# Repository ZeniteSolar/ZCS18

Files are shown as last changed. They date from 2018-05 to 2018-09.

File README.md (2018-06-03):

# ZCS18 - Zênite CAN! Shield 2018
The piece of hardware used in almost all modules in the boat of Zênite Solar Team on 2018.

## About

zenite_logo 

[Zênite Solar TEAM](https://github.com/ZeniteSolar) is an universitary project from [IFSC](http://www.ifsc.edu.br) focused on the development of a high performance solar boat for races and it aims to be completly open source.

- All the hardware was developed using [KiCad](http://kicad-pcb.org/);
- Simulations was done using [LTSpice](http://www.analog.com/en/design-center/design-tools-and-calculators/ltspice-simulator.html);
- Schematics are available [here][Schematic];
- BOM are available [here][BOM];

## Status

- [x] Simulations
- [x] Schematics
- [x] PCB
- [x] Fabrication
- [ ] Assembly
- [ ] Test
- [ ] Basic Firmware for reference

## Board View

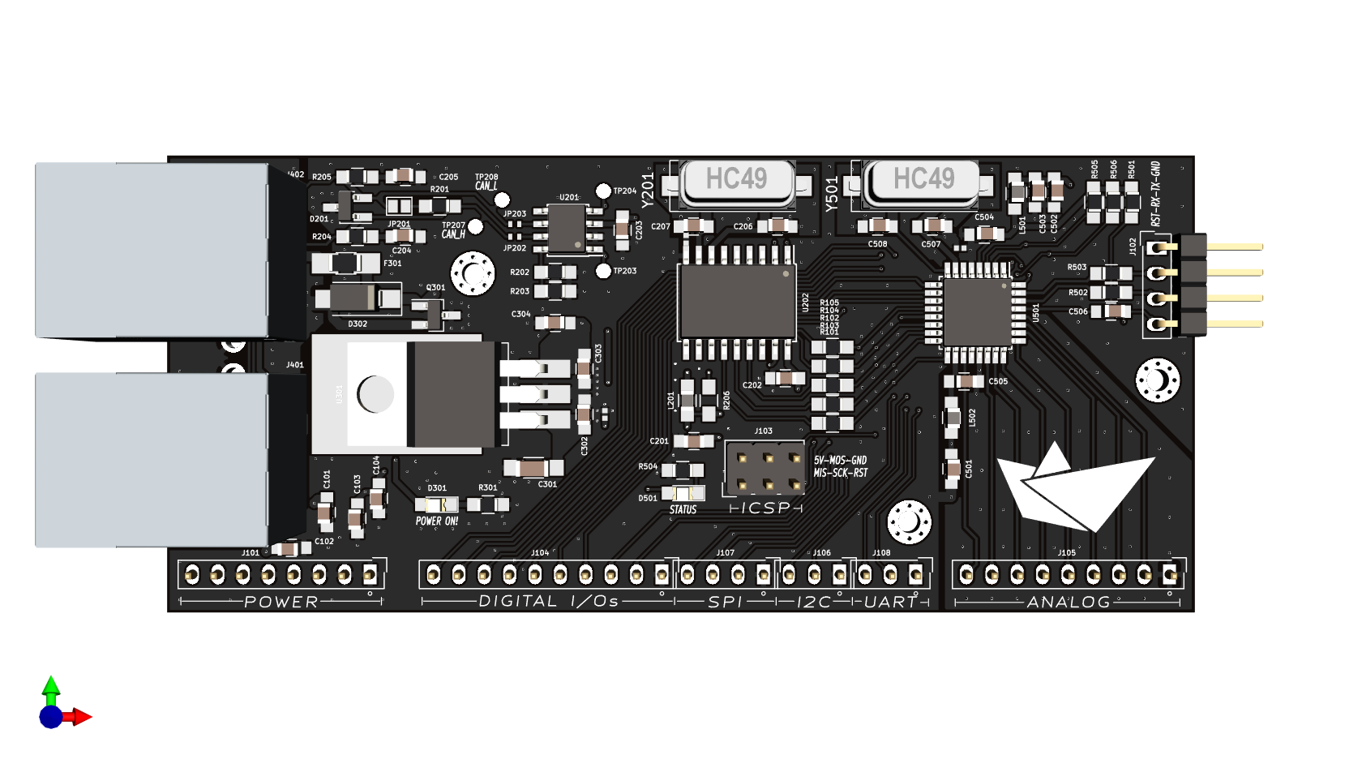
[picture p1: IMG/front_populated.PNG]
kicad3d_front_populated
 

***

[Schematic]: PDF/atmega_can_shield.pdf "Schematics"
[BOM]: PDF/BOM.pdf "Bill Of Materials"
[photo_front]: IMG/front.PNG "Fabricated Front"
[photo_back]: IMG/front.PNG "Fabricated Back"
[photo_front]: IMG/front.PNG "Populated Front"
[photo_back]: IMG/front.PNG "Populated Back"
[kicad3d_front]: IMG/front.PNG "Kicad Front"
[kicad3d_back]: IMG/back.PNG "Kicad Back"
[kicad3d_front_populated]: IMG/front_populated.PNG "Kicad Populated Front"
[kicad3d_back_populated]: IMG/back_populated.PNG "Kicad Populated Back"
[kicad3d_populated_angled]: IMG/populated_angled.PNG "Kicad Populated Board 3D View"
[zenite_logo]: https://avatars2.githubusercontent.com/u/8411347?s=100 "Zênite Solar Team Logo"

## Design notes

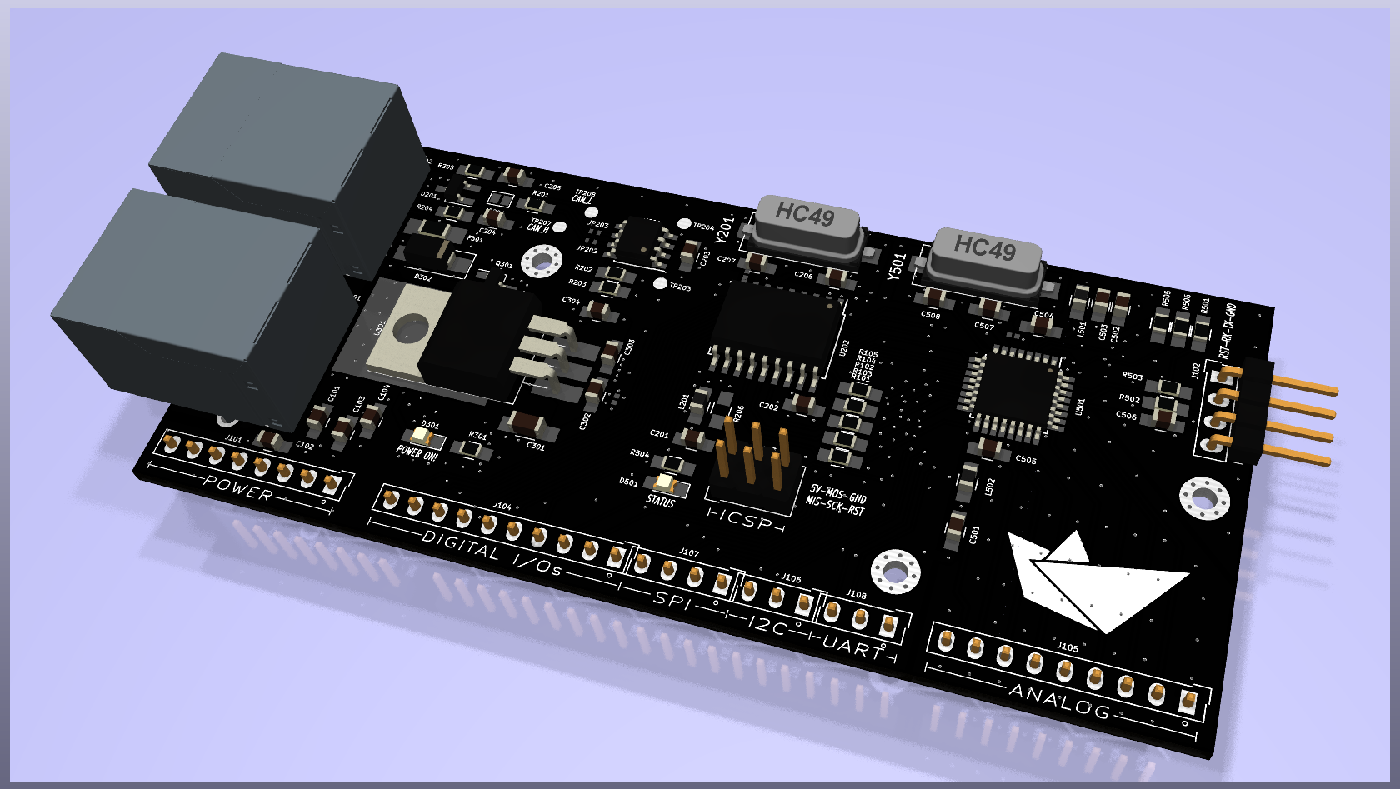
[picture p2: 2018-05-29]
IMG/populated_angled.PNG

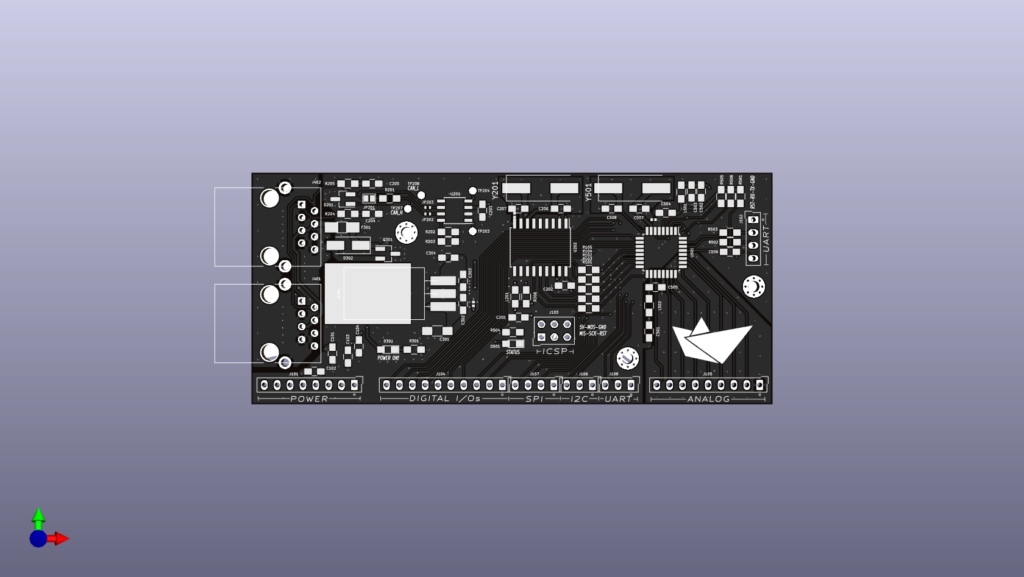
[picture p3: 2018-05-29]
IMG/front.PNG

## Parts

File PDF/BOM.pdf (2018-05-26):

atmega_can_shield_bom_João A.C.

CompPart | References | Value | Footprint | QTD Voltage
1 C_Small | | 100n | C_0805_HandSoldering | 12 >25V
2 CP1_Small | C301 | 10uF | C_1206_HandSoldering | 1 >25V
3 C_Small | C101 C103 C503 1u | C_0805_HandSoldering | 3 >25V
4 CP1_Small | C304 | 1uF | C_0805_HandSoldering | 1
5 C_Small | | 22pF | C_0805_HandSoldering | 4
6 C_Small | C204 C205 | 560p | C_0805_HandSoldering | 2
7LED_Small_ALT | D301 D501 | LED_RED | LED_0805_HandSoldering | 2
8 D_TVS | D302 | | D_SMA_Handsoldering | 1
9 D_TVS_x2_AAC | D201 | pesd1can | SOT-23_Handsoldering | 1
10 Fuse_Small | F301 | | Fuse_SMD1206_HandSolde | 1
11 CONN_01X09 | J105 | ANALOG | SL-109-X-XX_1x09 | 1
12 CONN_01X10 | J104 | DIGITAL I/Os SL-110-X-XX_1x10 | 1
13 CONN_01X03 | J106 | I2C | SL-103-X-XX_1x03 | 1
14 CONN_02X03 | J103 | ICSP | SDL-106-X-XX_2x03 | 1
15 GS2 | J201 J301 J501 | NetTie | \xc2\xb5NetTie-I_Connect | 3
16 RJ45 | J401 J402 | RJ45 | RJ45_YH59_01 | 2
17 CONN_01X04 | J107 | SPI | SL-104-X-XX_1x04 | 1
18 CONN_01X08 | J101 | SUPPLY | SL-108-X-XX_1x08 | 1
19 CONN_01X04 | J102 | USART | SL-104-X-XX_1x04 | 1
20 CONN_01X03 | J108 | USART | SL-103-X-XX_1x03 | 1
21 2-pole | open | | JP202 JP203 | 1
22Jumper_NO_Small JP201 | Termination GS2 | 1
23L_Core_Ferrite | L201 L501 L502 | 10uH | L_0805_HandSoldering | 3
24 Q_NMOS_GSD | Q301 | si2308cds | SOT-23_Handsoldering | 1
25 R_Small | 100 R_0805_HandSoldering | 7
26 R_Small | | 10k | R_0805_HandSoldering | 8
27 R_Small | R201 | 120 R_0805_HandSoldering | 1
28 R_Small | R502 R503 | 1k | R_0805_HandSoldering | 2
29 | U501 | | TQFP-32_7x7mm_Pitch0.8 | 1
30 | U202 | | SOIC-18W_7.5x11.6mm_Pi | 1
31 MCP2551-I_SN | U201 | MCP2561 | SOIC-8_3.9x4.9mm_Pitch1 | 1
32LM7805_TO220 | U301 | | TO-220_Horizontal_SMD | 1
33 Crystal_Small | Y201 Y501 | 16MHz | Crystal_SMD_HC49_4HSM | 2

C102 C104 C201
C202 C203 C302
C303 C501 C502
C504 C505 C506

C206 C207 C507
C508

TVS 24V
400W

500mA
resettable

Jumper_2_O
pen

R101 R102 R103
R104 R105 R204
R205
R202 R203 R206
R301 R501 R504
R505 R506

SRAM 512B
EEPROM
ATMEGA328P-AU_alt

ATMEGA328
P-AU_alt

MCP2515-E_ST-SOIC18

MCP2515-
E/ST-SOIC18

VXO7805-
1000

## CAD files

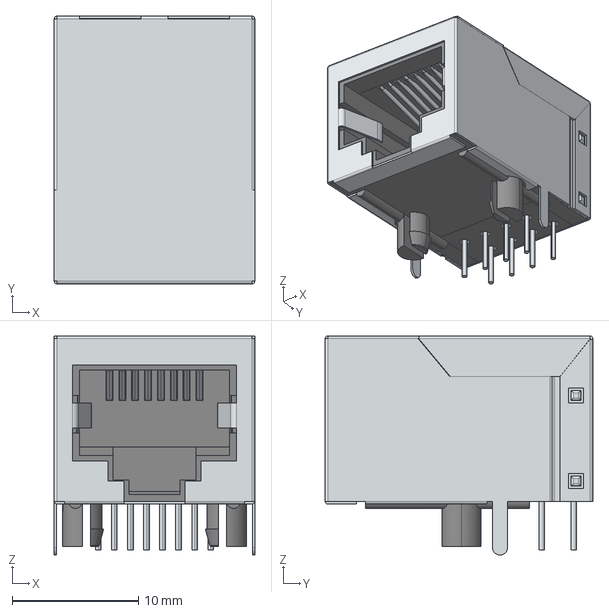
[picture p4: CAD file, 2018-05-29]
rj45.step
15.9 x 21.2 x 17.3 mm

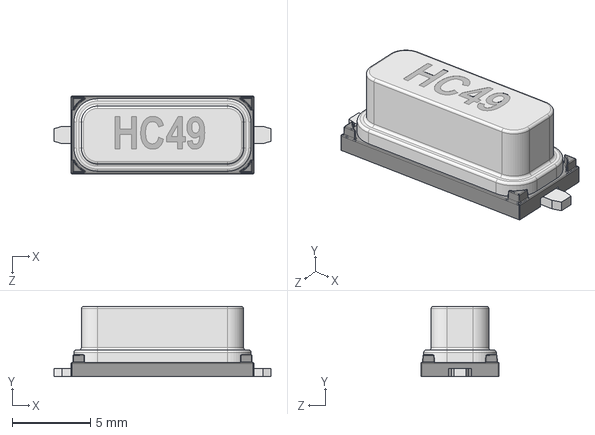
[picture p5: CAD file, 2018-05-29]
HC49.step
13.9 x 4.51 x 5.00 mm

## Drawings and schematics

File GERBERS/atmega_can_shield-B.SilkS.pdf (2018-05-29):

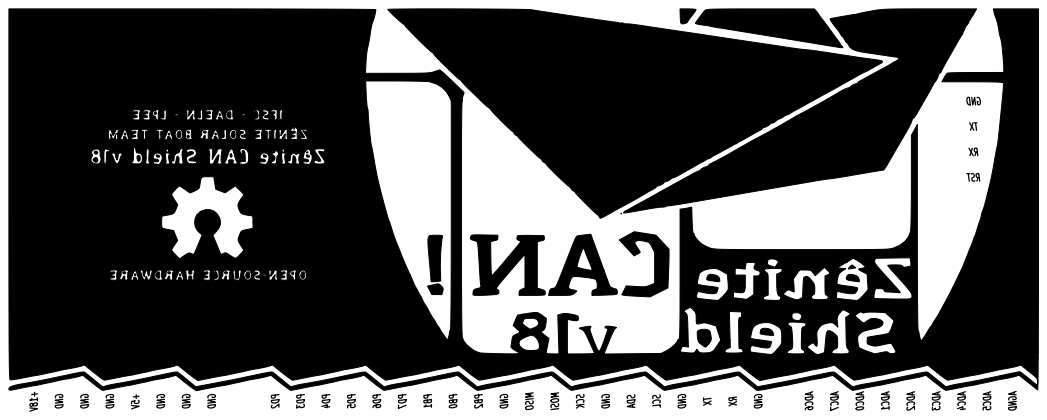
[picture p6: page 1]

TXRX GND ADC6 ADC7 ADC0 ADC1 ADC2 ADC3 ADC4 ADC5 +18V GND GND GND +5V GND GND GND GND GND AGND SCK SDA SCL TXRX PD2 PD3 PD4 PD5 PD6 PD7 PB1 PB0 PB2 GND MISO MOSI

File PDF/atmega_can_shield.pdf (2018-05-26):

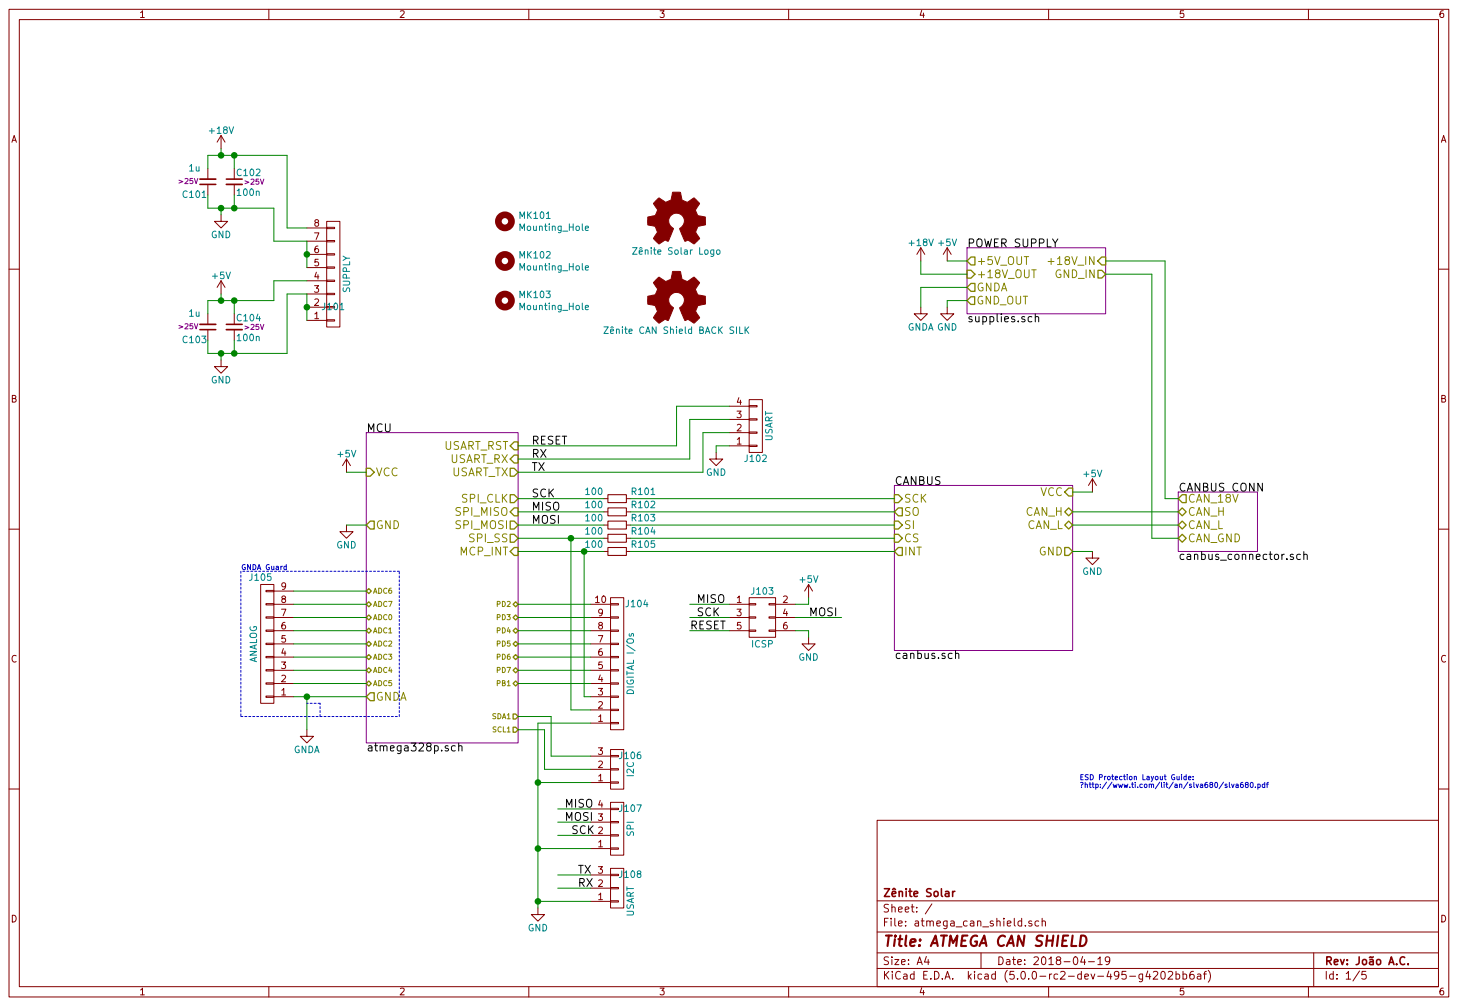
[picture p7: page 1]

Zênite Solar Logo Zênite CAN Shield BACK SILK

100 R102
100 R103

CAN_18V CAN_GND

ESD Protection Layout Guide:

File: atmega_can_shield.sch Sheet: / Zênite Solar

Id: 1/5 Title: ATMEGA CAN SHIELD

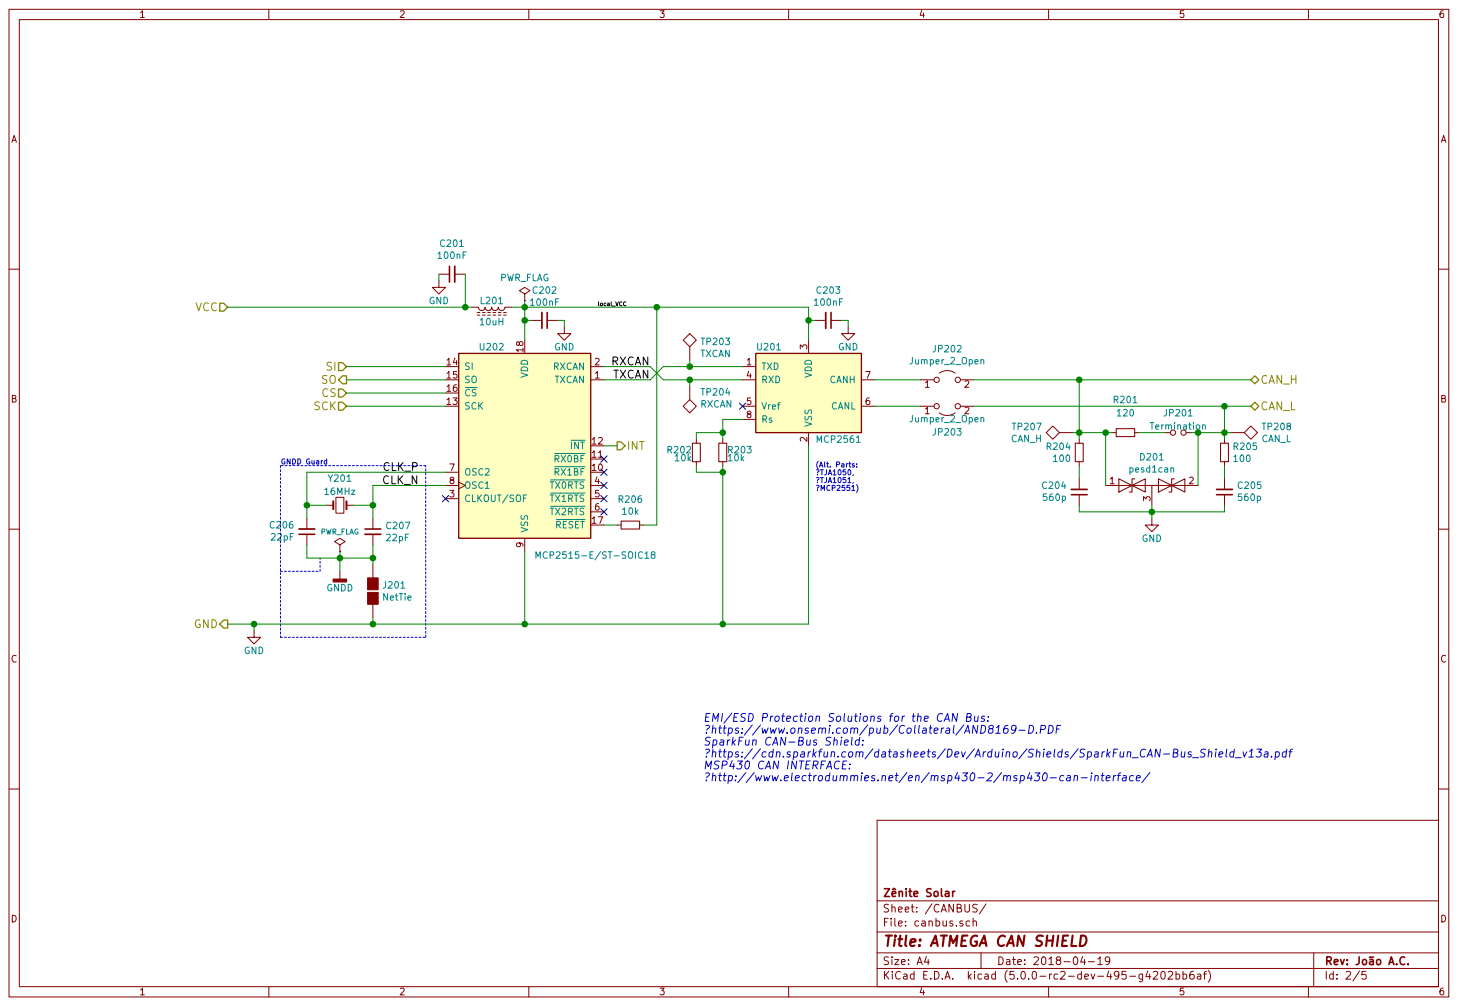
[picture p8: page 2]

3 RXD 4 Vref 5 CANL 6 CANH 7 Rs 8 U201 MCP2561 TXCAN
RXCAN

EMI/ESD Protection Solutions for the CAN Bus:
https://www.onsemi.com/pub/Collateral/AND8169-D.PDF
SparkFun CAN-Bus Shield:
https://cdn.sparkfun.com/datasheets/Dev/Arduino/Shields/SparkFun_CAN-Bus_Shield_v13a.pdf
MSP430 CAN INTERFACE:
http://www.electrodummies.net/en/msp430-2/msp430-can-interface/

File: canbus.sch Sheet: /CANBUS/ Zênite Solar

Id: 2/5 Title: ATMEGA CAN SHIELD

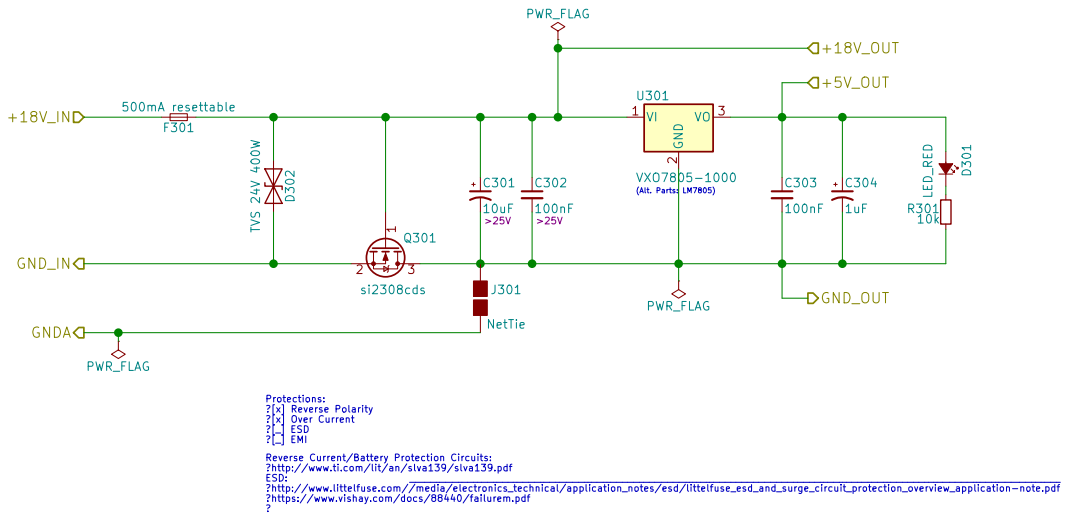
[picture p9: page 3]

si2308cds Reverse Current/Battery Protection Circuits:

https://www.vishay.com/docs/88440/failurem.pdf Protections:
[x] Reverse Polarity
[x] Over Current
[_] ESD

http://www.ti.com/lit/an/slva139/slva139.pdf ESD:
http://www.littelfuse.com//media/electronics_technical/application_notes/esd/littelfuse_esd_and_surge_circuit_protection_overview_application-note.pdf

File: supplies.sch Sheet: /POWER SUPPLY/ Zênite Solar

Id: 3/5 Title: ATMEGA CAN SHIELD

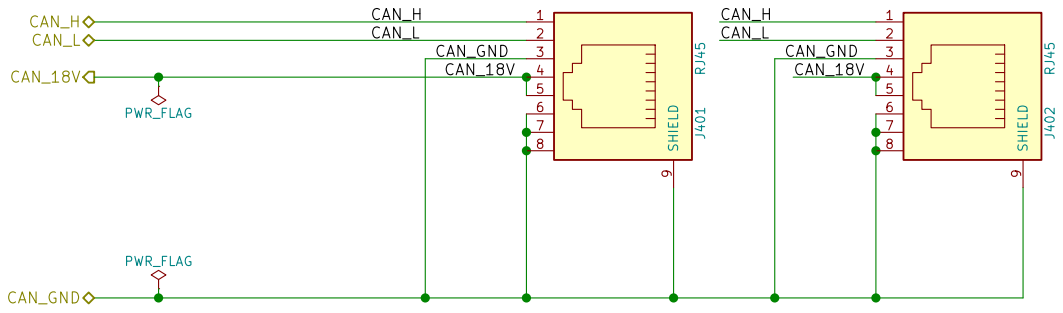
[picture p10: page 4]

File: canbus_connector.sch Sheet: /CANBUS CONN/ Zênite Solar

Id: 4/5 Title: ATMEGA CAN SHIELD

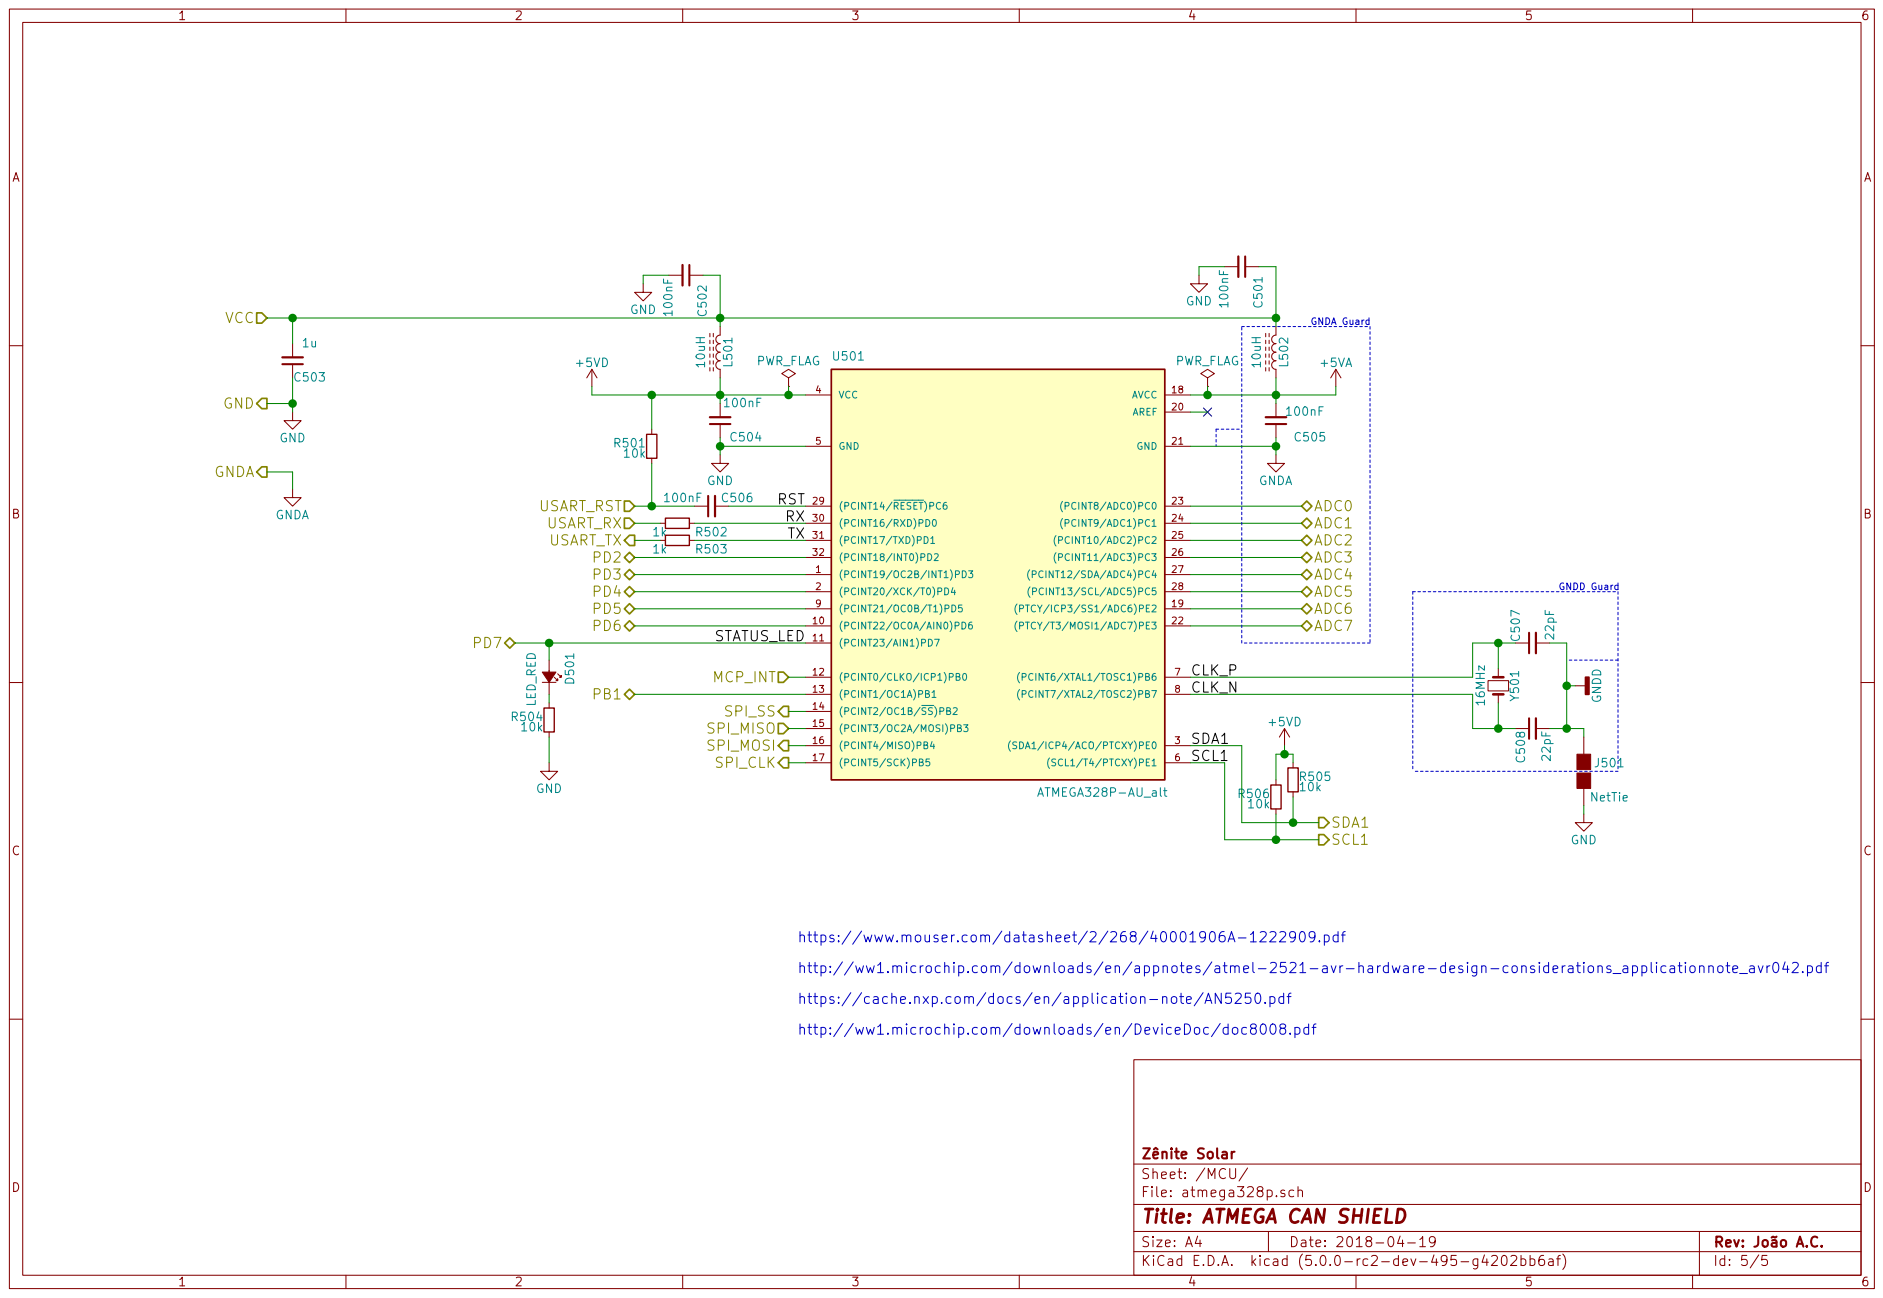
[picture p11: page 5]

https://www.mouser.com/datasheet/2/268/40001906A-1222909.pdf
http://ww1.microchip.com/downloads/en/appnotes/atmel-2521-avr-hardware-design-considerations_applicationnote_avr042.pdf
https://cache.nxp.com/docs/en/application-note/AN5250.pdf

Id: 5/5 Title: ATMEGA CAN SHIELD

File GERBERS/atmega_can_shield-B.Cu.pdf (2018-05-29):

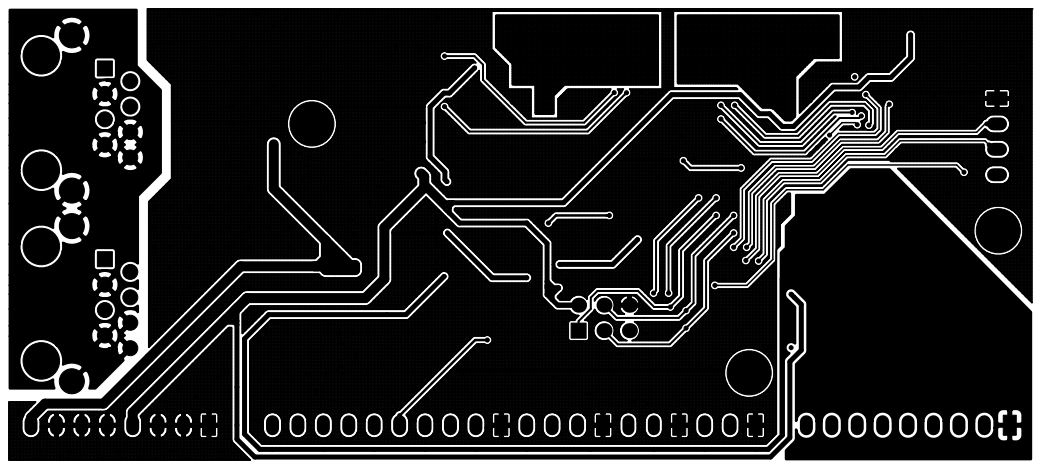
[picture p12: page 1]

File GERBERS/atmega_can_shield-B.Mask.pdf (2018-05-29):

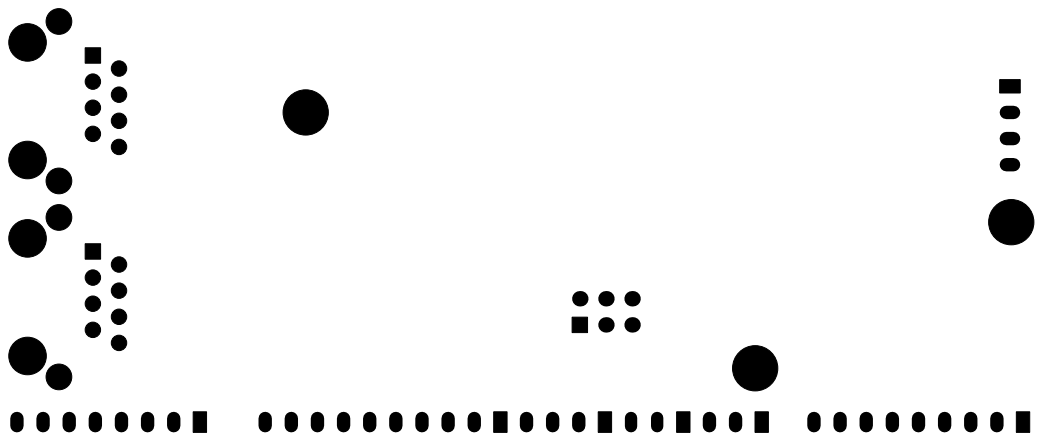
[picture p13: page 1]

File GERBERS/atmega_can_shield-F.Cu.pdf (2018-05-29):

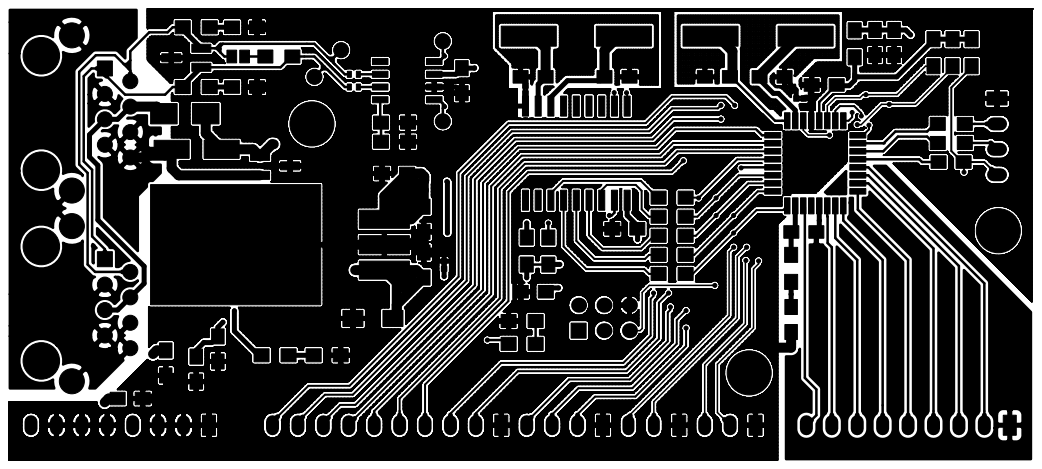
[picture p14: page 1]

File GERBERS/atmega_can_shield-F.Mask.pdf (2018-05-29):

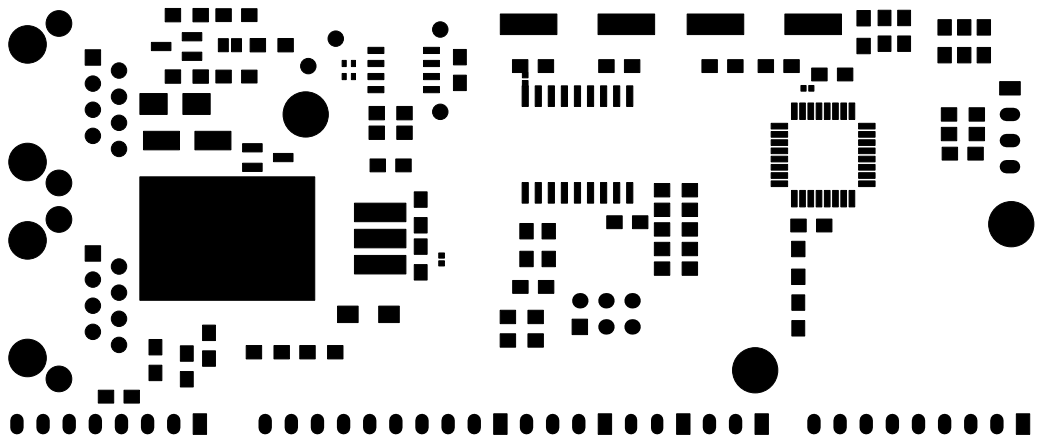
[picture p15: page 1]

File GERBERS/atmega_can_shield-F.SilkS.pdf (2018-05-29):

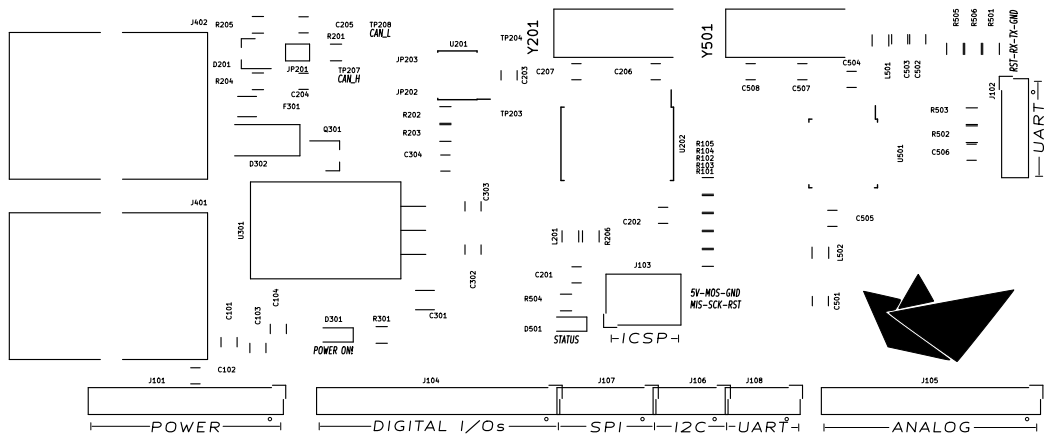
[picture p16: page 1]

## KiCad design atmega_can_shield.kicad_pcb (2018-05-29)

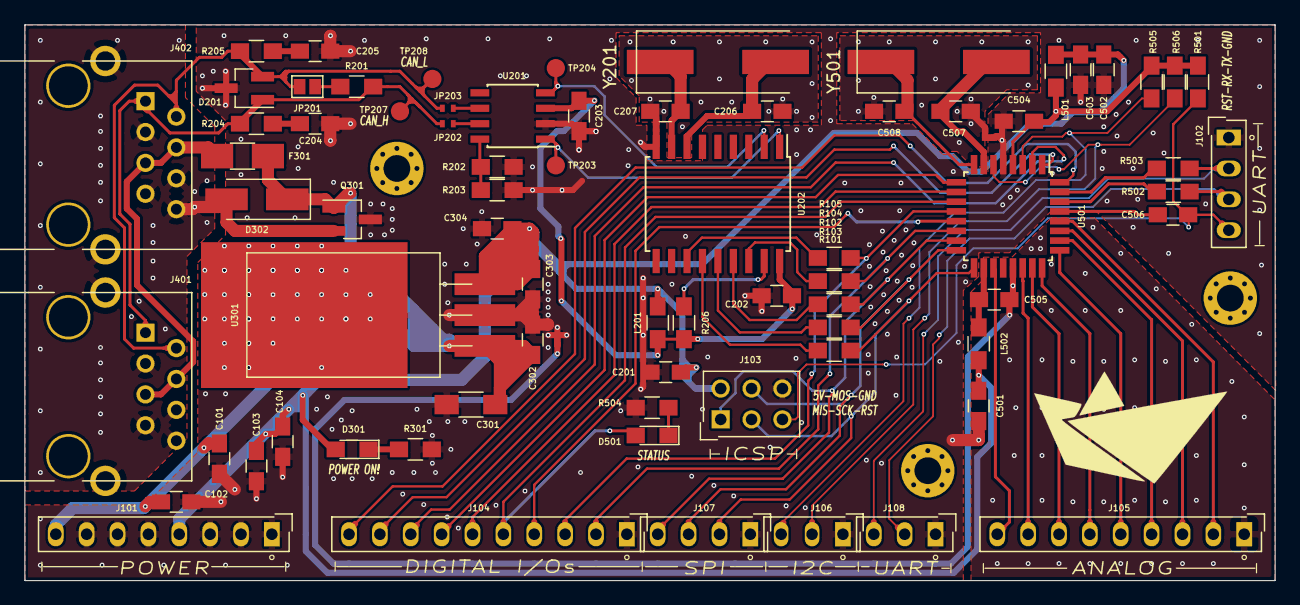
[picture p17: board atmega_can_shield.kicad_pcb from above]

Board: 2 copper layers, 102.9 x 45.7 mm, 79 parts (0 on the bottom side), 60 nets.

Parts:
C101, C103, C503: 1u; C_0805_HandSoldering
C102, C104: 100n; C_0805_HandSoldering
C201, C202, C203, C302, C303, C501, C502, C504, C505, C506: 100nF; C_0805_HandSoldering
C204, C205: 560p; C_0805_HandSoldering
C206, C207, C507, C508: 22pF; C_0805_HandSoldering
C301: 10uF; C_1206_HandSoldering
C304: 1uF; C_0805_HandSoldering
D201: pesd1can; SOT-23_Handsoldering
D301, D501: LED_RED; LED_0805_HandSoldering
D302: TVS 24V 400W; D_SMA_Handsoldering
F301: 500mA resettable; Fuse_SMD1206_HandSoldering
J101: SUPPLY; SL-108-X-XX_1x08
J102: USART; SL-104-X-XX_1x04
J103: ICSP; SDL-106-X-XX_2x03
J104: DIGITAL I/Os; SL-110-X-XX_1x10
J105: ANALOG; SL-109-X-XX_1x09
J106: I2C; SL-103-X-XX_1x03
J107: SPI; SL-104-X-XX_1x04
J108: USART; SL-103-X-XX_1x03
J201, J301, J501: NetTie; µNetTie-I_Connected_SMD
J401, J402: RJ45; RJ45_YH59_01
JP201: Termination; GS2
JP202, JP203: Jumper_2_Open; R_0402_NoSilk
L201, L501, L502: 10uH; L_0805_HandSoldering
MK101, MK102, MK103: Mounting_Hole; MountingHole_2.2mm_M2_Pad_Via
Q301: si2308cds; SOT-23_Handsoldering
R101, R102, R103, R104, R105, R204, R205: 100; R_0805_HandSoldering
R201: 120; R_0805_HandSoldering
R202, R203, R206, R301, R501, R504, R505, R506: 10k; R_0805_HandSoldering
R502, R503: 1k; R_0805_HandSoldering
TP203: TXCAN; Measurement_Point_Round-SMD-Pad_Small
TP204: RXCAN; Measurement_Point_Round-SMD-Pad_Small
TP207: CAN_H; Measurement_Point_Round-SMD-Pad_Small
TP208: CAN_L; Measurement_Point_Round-SMD-Pad_Small
U201: MCP2551-I/SN; SOIC-8_3.9x4.9mm_Pitch1.27mm
U202: MCP2515-E/ST-SOIC18; SOIC-18W_7.5x11.6mm_Pitch1.27mm
U301: LM7805; TO-220_Horizontal_SMD
U501: ATMEGA328P-AU_alt; TQFP-32_7x7mm_Pitch0.8mm
Y201, Y501: 16MHz; Crystal_SMD_HC49_4HSMX

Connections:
+5V: C103.2, C104.1, C201.2, C303.1, C304.1, C501.1, C502.1, C503.2, D301.2, J101.4, J103.2, L201.2, L501.2, L502.2, U301.3
+5VA: C505.2, L502.1, U501.18
+5VD: C504.2, L501.1, R501.1, R505.1, R506.1, U501.4
+18V: C101.2, C102.1, C301.1, C302.1, D302.1, F301.2, J101.8, Q301.1, U301.1
/CANBUS CONN/CAN_GND: D302.2, J401.3, J401.6, J401.7, J401.8, J401.9, J402.3, J402.6, J402.7, J402.8, J402.9, Q301.2
/CANBUS CONN/CAN_H: D201.1, J401.1, J402.1, JP202.2, R201.2, R204.1, TP207.1
/CANBUS CONN/CAN_L: D201.2, J401.2, J402.2, JP201.2, JP203.2, R205.1, TP208.1
/CANBUS/CLK_N: C207.1, U202.8, Y201.1
/CANBUS/CLK_P: C206.2, U202.7, Y201.2
/CANBUS/CS: R104.1, U202.16
/CANBUS/INT: R105.1, U202.12
/CANBUS/RXCAN: TP204.1, U201.4, U202.2
/CANBUS/SCK: R101.1, U202.13
/CANBUS/SI: R103.1, U202.14
/CANBUS/SO: R102.1, U202.15
/CANBUS/TXCAN: TP203.1, U201.1, U202.1
/CANBUS/local_VCC: C202.2, C203.2, L201.1, R206.1, U201.3, U202.18
/MCU/ADC0: J105.7, U501.23
/MCU/ADC1: J105.6, U501.24
/MCU/ADC2: J105.5, U501.25
/MCU/ADC3: J105.4, U501.26
/MCU/ADC4: J105.3, U501.27
/MCU/ADC5: J105.2, U501.28
/MCU/ADC6: J105.9, U501.19
/MCU/ADC7: J105.8, U501.22
/MCU/CLK_N: C508.1, U501.8, Y501.1
/MCU/CLK_P: C507.1, U501.7, Y501.2
/MCU/MCP_INT: J104.3, R105.2, U501.12
/MCU/PB1: J104.4, U501.13
/MCU/PD2: J104.10, U501.32
/MCU/PD3: J104.9, U501.1
/MCU/PD4: J104.8, U501.2
/MCU/PD5: J104.7, U501.9
/MCU/PD6: J104.6, U501.10
/MCU/PD7: D501.2, J104.5, U501.11
/MCU/RST: C506.2, U501.29
/MCU/RX: R502.1, U501.30
/MCU/SCL1: J106.2, R506.2, U501.6
/MCU/SDA1: J106.3, R505.2, U501.3
/MCU/SPI_SS: J104.2, R104.2, U501.14
/MCU/TX: R503.1, U501.31
/MISO: J103.1, J107.4, R102.2, U501.15
/MOSI: J103.4, J107.3, R103.2, U501.16
/POWER SUPPLY/+18V_IN: F301.1, J401.4, J401.5, J402.4, J402.5
/RESET: C506.1, J102.4, J103.5, R501.2
/RX: J102.3, J108.2, R502.2
/SCK: J103.3, J107.2, R101.2, U501.17
/TX: J102.2, J108.3, R503.2
GND: C101.1, C102.2, C103.1, C104.2, C201.1, C202.1, C203.1, C204.1, C205.1, C301.2, C302.2, C303.2, C304.2, C501.2, C502.2, C503.1, C504.1, D201.3, J101.1, J101.2, J101.3, J101.5, J101.6, J101.7, J102.1, J103.6, J104.1, J106.1, J107.1, J108.1, J201.2, J301.1, J501.2, Q301.3, R202.2, R203.2, R301.2, R504.2, U201.2, U202.9, U301.2, U501.5
GNDA: C505.1, J105.1, J301.2, U501.21
GNDD: C206.1, C207.2, C507.2, C508.2, J201.1, J501.1
unnamed: C204.2, R204.2
unnamed: C205.2, R205.2
unnamed: D301.1, R301.1
unnamed: D501.1, R504.1
unnamed: JP201.1, R201.1
unnamed: JP202.1, U201.7
unnamed: JP203.1, U201.6
unnamed: R202.1, R203.1, U201.8
unnamed: R206.2, U202.17

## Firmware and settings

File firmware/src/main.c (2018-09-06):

// coding: utf-8

#include "main.h"

void init(void)
{
    #ifdef WATCHDOG_ON
        wdt_init();
    #endif 
 
    #ifdef USART_ON
        usart_init(MYUBRR,1,1);                         // inicializa a usart
        VERBOSE_MSG_INIT(usart_send_string("\n\n\nUSART... OK!\n"));
    #endif

    #ifdef WATCHDOG_ON
        VERBOSE_MSG_INIT(usart_send_string("WATCHDOG..."));
        wdt_reset();
        VERBOSE_MSG_INIT(usart_send_string(" OK!\n"));
    #else
        VERBOSE_MSG_INIT(usart_send_string("WATCHDOG... OFF!\n"));
    #endif

    #ifdef PWM_ON
        VERBOSE_MSG_INIT(usart_send_string("PWM..."));
        pwm_init();
        VERBOSE_MSG_INIT(usart_send_string(" OK!\n"));
    #else
        VERBOSE_MSG_INIT(usart_send_string("PWM... OFF!\n"));
    #endif

    #ifdef WATCHDOG_ON
        wdt_reset();
    #endif

    #ifdef CAN_ON
        VERBOSE_MSG_INIT(usart_send_string("CAN (500kbps)..."));
        can_init(BITRATE_500_KBPS);
        VERBOSE_MSG_INIT(usart_send_string(" OK!\n"));
        VERBOSE_MSG_INIT(usart_send_string("CAN filters..."));
        //can_static_filter(can_filter);
        VERBOSE_MSG_INIT(usart_send_string(" OK!\n"));
    #else
        VERBOSE_MSG_INIT(usart_send_string("CAN... OFF!\n"));
    #endif

    #ifdef WATCHDOG_ON
        wdt_reset();
    #endif

    #ifdef ADC_ON
        VERBOSE_MSG_INIT(usart_send_string("ADC..."));
        adc_init();
        VERBOSE_MSG_INIT(usart_send_string(" OK!\n"));
    #else
        VERBOSE_MSG_INIT(usart_send_string("ADC... OFF!\n"));
    #endif

    #ifdef WATCHDOG_ON
        wdt_reset();
    #endif

    #ifdef SLEEP_ON 
        VERBOSE_MSG_INIT(usart_send_string("SLEEP..."));
        sleep_init();
        VERBOSE_MSG_INIT(usart_send_string(" OK!\n"));
    #else
        VERBOSE_MSG_INIT(usart_send_string("SLEEP... OFF!\n"));
    #endif

    #ifdef WATCHDOG_ON
        wdt_reset();
    #endif

 	#ifdef MACHINE_ON
        VERBOSE_MSG_INIT(usart_send_string("MACHINE..."));
		machine_init();
        VERBOSE_MSG_INIT(usart_send_string(" OK!\n"));
    #else
        VERBOSE_MSG_INIT(usart_send_string("MACHINE... OFF!\n"));
	#endif

    #ifdef WATCHDOG_ON
        wdt_reset();
    #endif
	
    #ifdef LED_ON
        set_bit(LED_DDR, LED);                      // LED como saída
        VERBOSE_MSG_INIT(usart_send_string("LED... OK!\n"));
    #else
        VERBOSE_MSG_INIT(usart_send_string("LED... OFF!\n"));
    #endif

    #ifdef WATCHDOG_ON
        wdt_reset();
    #endif

	
    // ------------------------------------------------------------------------
#ifdef ENABLE_HARDWARE_OVERVOLTAGE_INTERRUPT
	clr_bit(BatOverVoltageInterrupt_DDR,BatOverVoltageInterrupt);	// int0 as input
	clr_bit(BatOverVoltageInterrupt_PORT,BatOverVoltageInterrupt);	// int0 without pullpup
    EICRA |= (1<<ISC01) | (1<<ISC00);           // rising edge for int0
    EIMSK |= (1<<INT0);                         // enables int0 interrupt
    EIFR |= (1<<INTF0);                         // clears int0 interrupt
#endif // ENABLE_HARDWARE_OVERVOLTAGE_INTERRUPT 
 
#ifdef ENABLE_HARDWARE_ENABLE_SWITCH_INTERRUPT   
	clr_bit(Enable_DDR,Enable);					// int1 as input
	set_bit(Enable_PORT,Enable);				// int1 with pullup
    EICRA |= (0<<ISC11) | (0<<ISC10);           // low level for int1
    //EIMSK |= (1<<INT1);                         // enables int1 interrupt
    EIFR |= (1<<INTF1);                         // clears int1 interrupt
#endif // ENABLE_HARDWARE_ENABLE_SWITCH_INTERRUPT

#ifdef MACHINE_ON
    print_configurations();
#endif // MACHINE_ON

    sei();
}

int main(void)
{

    init();
   
	for(;;){
		#ifdef WATCHDOG_ON
            wdt_reset();
		#endif

        #ifdef MACHINE_ON
            machine_run();
        #else
            #ifdef PWM_ON
                #ifdef PWM_TEST
                    #ifdef CONVERTER_TEST_WITH_FIXED_DUTYCYCLE
                        set_pwm_duty_cycle(CONVERTER_TEST_WITH_FIXED_DUTYCYCLE_DT_VALUE);
                    #else
                        static uint8_t i = 0;
                        set_pwm_duty_cycle(i++);
                        if(i>PWM_D_MAX) i = PWM_D_MIN;
                    #endif
                #else
                    #ifdef PEO_TEST
                        read_and_check_adcs();
                        pwm_compute();
                    #endif
                #endif
            #endif
        #endif

		#ifdef SLEEP_ON
            sleep_mode();
		#endif
	}
}


/**
 * @brief se em debug, fica chaveando os pinos de debugs até o reset do watchdog
 */
ISR(BADISR_vect)
{
    for(;;){
        pwm_reset();
        VERBOSE_MSG_ERROR(usart_send_string("\nFATAL ERROR: BAD ISR."));
        #ifdef WATCHDOG_ON
            VERBOSE_MSG_ERROR(usart_send_string("WAITING FOR WATCHDOG TO RESET...\n"));
        #endif
        #ifdef DEBUG_ON
            DEBUG0;
            DEBUG1;
            _delay_ms(100);
        #endif
    }
}

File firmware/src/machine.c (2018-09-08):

#include "machine.h"

/*
 *
 */

/**
 * @brief 
 */
void machine_init(void)
{
	//clr_bit(PRR0, PRTIM2);                          // Activates clock

    // MODE 2 -> CTC with TOP on OCR1
    TCCR2A  =    (1 << WGM21) | (0 << WGM20)        // mode 2
              | (0 << COM2B1) | (0 << COM2B0)       // do nothing
              | (0 << COM2A1) | (0 << COM2A0);      // do nothing

    //clr_bit(DDRB, PB3); // output for frequency debug

    TCCR2B =
#if MACHINE_TIMER_PRESCALER ==     1
                (0 << CS22) | (0 << CS21) | (1 << CS20) // Prescaler N=1
#elif MACHINE_TIMER_PRESCALER ==   8
                (0 << CS22) | (1 << CS21) | (0 << CS20) // Prescaler N=8
#elif MACHINE_TIMER_PRESCALER ==   32
                (0 << CS22) | (1 << CS21) | (1 << CS20) // Prescaler N=32
#elif MACHINE_TIMER_PRESCALER ==   64
                (1 << CS22) | (0 << CS21) | (0 << CS20) // Prescaler N=64
#elif MACHINE_TIMER_PRESCALER ==   128
                (1 << CS22) | (0 << CS21) | (1 << CS20) // Prescaler N=128
#elif MACHINE_TIMER_PRESCALER ==   256
                (1 << CS22) | (1 << CS21) | (0 << CS20) // Prescaler N=256
#elif MACHINE_TIMER_PRESCALER ==   1024
                (1 << CS22) | (1 << CS21) | (1 << CS20) // Prescaler N=1024
#else
                0
#endif
                | (0 << WGM22);      // mode 2

    OCR2A = MACHINE_TIMER_TOP;                       // OCR2A = TOP = fcpu/(N*2*f) -1

    TIMSK2 |=   (1 << OCIE2A);                      // Activates interruption

    set_machine_initial_state();
    set_state_initializing();
} 

/**
 * @brief set machine initial state
 */
inline void set_machine_initial_state(void)
{
#ifdef CAN_ON
    system_flags.mppt_on = 1;
#else
    system_flags.mppt_on = 0;
#endif // CAN_ON
    system_flags.enable = 0;

    error_flags.all = 0;

    control.D = 0;
    control.D_step = PWM_D_STEP;
    control.pi_limit = 0;
    control.updown = 0;
    control.vi[0] = control.vi[1] = 0;
    control.ii[0] = control.ii[1] = 0;
    control.pi[0] = control.pi[1] = 0;
    control.vo[0] = control.vo[1] = 0;
    control.io[0] = control.io[1] = 0;
    control.po[0] = control.po[1] = 0;
    control.dvi = control.dvo = control.dii = control.dio = control.dpi = 0;
    control.mpp_vi = control.mpp_ii = control.mpp_pi = control.mpp_D = 0;

    machine_clk = machine_clk_divider = led_clk_div = 0;
    something_changed = 0;
}

/**
* @brief read and checks current levels
*/
inline void read_and_check_adcs(void)
{ 
#ifdef ADC_ON
    //calc_avg();
    uint64_t tmp;
    tmp = (uint64_t)(uint16_t)AVG_PANEL_VOLTAGE * (uint32_t)ADC_PANEL_VOLTAGE_ANGULAR_COEF ;
    control.vi[0] = tmp >> 10;
//        +ADC_PANEL_VOLTAGE_LINEAR_COEF;
    tmp = (uint64_t)(uint16_t)AVG_PANEL_CURRENT * (uint32_t)ADC_PANEL_CURRENT_ANGULAR_COEF ; 
    control.ii[0] = tmp >> 10;
//        +ADC_PANEL_CURRENT_LINEAR_COEF;
    tmp = (uint64_t)(uint16_t)AVG_BATTERY_VOLTAGE * (uint32_t)ADC_BATTERY_VOLTAGE_ANGULAR_COEF ; 
    control.vo[0] = tmp >> 10;
//        +ADC_BATTERY_VOLTAGE_LINEAR_COEF;

    switch(state_machine){
        default:
        case STATE_INITIALIZING:
#ifdef CHECK_INITIALIZING_CONDITIONS
            check_initializing_panel_voltage();
            check_initializing_panel_current();
            check_initializing_battery_voltage();
#endif // CHECK_INITIALIZING_CONDITIONS

            break;
        case STATE_IDLE:
#ifdef CHECK_IDLE_CONDITIONS
            check_idle_panel_voltage();
            check_idle_panel_current();
            check_idle_battery_voltage();
#endif //CHECK_IDLE_CONDITIONS

            break;
        case STATE_RUNNING:
#ifdef CHECK_RUNNING_CONDITIONS
            check_running_panel_voltage();
            check_running_panel_current();
            check_running_battery_voltage();
#endif // CHECK_RUNNING_CONDITIONS

            break;
    } 
#endif
 
}

/**
* @brief checks if the current level is ok for INITIALIZING state
*/
inline void check_initializing_panel_current(void)
{ 
    if(control.ii[0]> NOT_RUNNING_PANEL_CURRENT_MAX){
        // PANEL SHORTED 
        // or current sensor problem
        // there is no way to diagnose
        // -> error
        error_flags.panel_overcurrent = 1;
        VERBOSE_MSG_ERROR(usart_send_string("panel.overcurrent = 1\n"));
    }else if(control.ii[0]< NOT_RUNNING_PANEL_CURRENT_MIN){
        // PANEL OPEN 
        // -> ok
        error_flags.panel_overcurrent = 0;
        VERBOSE_MSG_ERROR(usart_send_string("panel.overcurrent = 0\n"));
    }
}

/**
 * @brief checks if the voltage level is ok for INITIALIZING state
 */
inline void check_initializing_panel_voltage(void)
{
    if(control.vi[0]> NOT_RUNNING_PANEL_VOLTAGE_MAX){
        // PANEL OVERVOLTAGE 
        // or panel voltage sensor damaged 
        // -> error
        error_flags.panel_overvoltage = 1;
        VERBOSE_MSG_ERROR(usart_send_string("panel.overvoltage = 1\n"));
    }else{
        error_flags.panel_overvoltage = 0;
        VERBOSE_MSG_ERROR(usart_send_string("panel.overvoltage = 0\n"));
    }

    if(control.vi[0]< NOT_RUNNING_PANEL_VOLTAGE_MIN){
        // PANEL DISCONNECTED 
        // or shorted: should check current
        // if panel current isn't above limits, 
        // the panel voltage sensor is damaged
        // -> error
        error_flags.panel_undervoltage = 1;
        VERBOSE_MSG_ERROR(usart_send_string("panel.undervoltage = 1\n"));
    }else{
        error_flags.panel_undervoltage = 0;
        VERBOSE_MSG_ERROR(usart_send_string("panel.undervoltage = 0\n"));
    }
}

/**
* @brief checks if the voltage of Battery level is ok for INITIALIZING state
*/
inline void check_initializing_battery_voltage(void)
{
    if(control.vo[0]> NOT_RUNNING_BATTERY_VOLTAGE_MAX){
        // BATTERY OVERVOLTAGE -> overcharged
        // or battery voltage sensor damaged
        // if it is thee case, it will not protect against overcharge.
        // -> error
        error_flags.battery_overvoltage = 1;
        VERBOSE_MSG_ERROR(usart_send_string("battery.overvoltage = 1\n"));
    }else{
        error_flags.battery_overvoltage = 0;
        VERBOSE_MSG_ERROR(usart_send_string("battery.overvoltage = 0\n"));
    }
        
    if(control.vo[0]< NOT_RUNNING_BATTERY_VOLTAGE_MIN ){
        // BATTERY UNDERVOLTAGE -> discharged
        // or battery voltage sensor damaged
        // if it is thee case, it will not protect against overcharge.
        // -> error
        error_flags.battery_undervoltage = 1;
        VERBOSE_MSG_ERROR(usart_send_string("battery.undervoltage = 1\n"));
    }else{
        error_flags.battery_undervoltage = 0;
        VERBOSE_MSG_ERROR(usart_send_string("battery.undervoltage = 0\n"));
    }

}


/**
 * @brief checks if the current level is ok for IDLE state
 */
inline void check_idle_panel_current(void)
{ 
   check_initializing_panel_current();
}

/**
 * @brief checks if the voltage level is ok for IDLE state
 */
inline void check_idle_panel_voltage(void)
{
    check_initializing_panel_voltage();
}
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

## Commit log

2018-05-26 First commit: the project was finished and mmanufactured (just the pcbs) but not tested nor documented yet.
    [analog.sch, atmega328p-2018-04-22-15-33-52.sch, atmega328p.sch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]
2018-05-29 Changed 3D to KiCAD 5 and exported .wrl file
    [HC49.step, atmega328p.sch, atmega_can_shield.kicad_pcb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]
2018-05-29 PCB material changed to black on .wrl file.
2018-05-29 .step files changed to .wrl
    [atmega_can_shield.kicad_pcb]
2018-07-20 Status led changed to new pin and added a blink pattern to main loop if MACHINE_ON isnt defined.
2018-07-20 ADC setted to 5kHz, some other minor improvements.
2018-07-20 USART, WATCHDOG, PWM, ADC working. Now testing machine
2018-07-20 ADC readings tested, ifdefs 8bits fixed
    [adc.c]
2018-07-20 ADC tested: OK. Reading 1021 at 5V, 0 at 0V
2018-07-22 PWM changed to mode 14 to get better resolution for 100kHz.
2018-07-22 added a print version for 32 bits unsigned
2018-07-30 Added precompiled PWM configurations. Tested -> OK
2018-08-24 adc_data_ready initialized in adc_init instead adc.h
2018-08-24 algorithm for zero power detection enhanced
2018-08-25 machine prints was causing clock conflict. Fixed
    [machine.c]
2018-08-27 last test night codes. adc avg was fixed, and peo was tested but not correctly working yet
    [PeO.c, adc.c, conf.h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]
2018-08-31 adc linearized to mV and mA with good precision, and ERROR detection was implemented, but not fully tested yet.
    [conf.h, machine.c, main.c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]
2018-09-02 organized to work with several configurations, aka sweep, p&o or just a fixed PWM
    [pwm.c, pwm.h]
2018-09-02 minor changes to test the power converter without checks and algorithms.
2018-09-04 ADC frequency is now configured at conf.h. ADC frequency was scaled up to 10khz working.
2018-09-04 multiplications for adc conversion was fixed by especifying the data types.
    [machine.c]
2018-09-05 algorithms fixed. every combination of configuration are OK (tested)
    [conf.h, machine.c, mppt.c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]
2018-09-06 input power and battery voltage software limitations included. Battery Voltage limitations was tested under simulated conditions (using 12V battery and DC power supply).
2018-09-06 small fixes for ifdefs logic
    [pwm.c]
2018-09-06 hardware battery overvoltage protection configured and tested just FINE.
2018-09-06 added pi max config print
2018-09-06 FAKE_ADC config added test logic without the power converter
